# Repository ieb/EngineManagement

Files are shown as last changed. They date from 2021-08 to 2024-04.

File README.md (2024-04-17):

# Engine Management 

In July 2021 my boat was hit by lightning. The Volvo Penta D2-40 MDI unit that manages the Engine, a Volvo Penta D2-40F failed badly leaving the starter motor engaged and nearly causing an engine fire.

# Main control board

Update 20240417: In service, no issues after 3 years.

(see pcb/EngineManagementSimpleWithRelays.sch )

This project is based on the standard wiring for the core engine which is a Perkins 100. In that form the engine is controlled by switches, relays and a few flyback diodes. The only part of the original engine control that survived the strike was the Volvo Penta buttons, so those are used by a control board with pnp transistors driving relays triggered by the original buttons pulling the base of the pnp to ground. PushOn/PushOff is provided by a latching relay unit based on a LED control chip that draws a few uA when off. The control circuit draws 0.5A max and is protected by a 5A fuse and 600W TVS which will blow the fuse in the event of a voltage surge.

The main relays for Start, Stop, Glow and aux are all standard iso 40A automotive relays, each circuit fused with a suitable fuse. 

There are basic alarms for oil pressure, charge and temperature with the temperature alarm using a differential op amp with high gain adjusted to turn on a pnp at a set temperature. These all drive a buzzer with LEDs to indicate the alarm. 

A standard Tachometer sensing from the alternator W+ provides rev and engine hours. These are almost disposable being 30 GBP on eBay from many sources, all 85mm same as the Volvo Penta Tachometer.

## Mosfet alternative

Update 20240417: The PCB was prototyped, but never put into service since the relay based control board has proved 100% reliable and in service for 3 years. This section is for reference.

Although the original MDI failed due to the MOSFETs going short circuit, and in this respect relays may be more robust, it should be possible to protect MOSFETs or at least fail safe.

A 1.5KW TVS (eg SMCJ14A) with a 14.0V revers standoff, 15.6V minimum breakdown will conduct 5A@16V, 10A@18V and 40A@20V, which makes it viable as protection for excessive voltages upto 40A current, aiming to blow a fuse at above those voltages. Each mosfet needs its own TVS + suitably sized fuse or breaker. In the event of a strike or surge the TVS will short and blow the fuse before damage is done even if the MOSFET is shorted. It wont work for currents greater than 40A without exceeding the max Vds voltage of the MOSFET below.

A SI7137DP-T1-GE3 has an on resistance of 0.0016 Ohms and will dissipate < 640mW for 20A when fully on. It, unfortunately has a Max Vds of 20V and Vgs of 12v so needs protection, but provided its protected represents a robust solution as a high level switch. 

In the relay board on/off was provided by a eBay relay board which used a LED controller. To keep the number of daughter boards to a minimum and save space this is replaced by a MAX15054 on-off controller driving a N-Channel mosfet which when turned on draws the gate of one of the SI7137's to near zero turning it fully on. The same N-Channel mosfet enables P-Channel mosfets connected to the gates of other SI7137s. When the VP buttons are pressed the gates of these mosfets are dragged down to 0v turning them on, and since the N-Channel mosfet is conducting the gate of the respective SI7137 is also dragged to 0v switching that mosfet on. All P-Channel gates are pulled to +ve, and all N-Channel gates are pulled to 0v. The SI7137 has a max source gate voltage of 12v and so a 10v zener with forward diode ensures that never gets over 11.5v. 

Simulations indicate that the power dissipation in the SI7137 at 20A is 2.5W, so a pair are used for the glow plugs. At 8A for the start and stop solenoids power dissipation is closer to 500mW. Board cooling pads are used, although it might be necessary to add chip heat sinks.

Since the SI7137 are 1/10th the size of the relays, the switching circuit and NMEA2000 interface controller will all fit onto a single 10cm x 15cm board (which is the size I have in stock).

All of the silicon components were available at Farnell except the SI7137's which were ordered from Mouser, airmailed from California. For some reason RS in the UK had no stock of any mosfets.

see pcb/EngineManagementWithMosfets.sch which includes a sub-sheet of the NMEA interface. There are LTSpice simulations in pcb/simulations/ of the mosfet layout confirming transient behavior, currents and power dissipation.

Since its likely that when there is a voltage spike something on the board will blow, assuming this board works, I'll probably make a batch and keep a few spares onboard the boat.

# NMEA2000 Interface

Update 20240417: In service, minor issues after 3 years, mostly surrounding message frequency and how to some parameters to display on standard instruments.

(see pcb/EngineManagement.sch)

The standard MDI talks J1939 which is the Diesel engine CAN standard protocol. Normally this communicates with other Volvo Penta instruments, but in my case this was only the Tachometer. The J1939 Volvo Penta Tachometer did not survive the strike. The CAN bus interface was destroyed, even though there was an attempt to protect if from surges. At over 500 GBP to replace, I decided to stick with the non J1939 tachometer from eBay. For details on how to drive J1939 see the main_deprecated.cpp file. Volvo Penta service technicians probably query the MDI for fault codes, but for owners there is limited benefit where the only unit is a tachometer or basic instruments.

Once I discovered the VP Tachometer was not repairable, a separate mechanical diesel to NMEA2000 board was designed and built around an Arduino Pro Mini (Atmel 328p MCU), MCP2515 CAN controller board and some passive components. There is just enough space on 328p to hold the code and run the controller and the data collected and emitted can be displayed on any NMEA2000 instrument (eg Raymarine e7 MFD).

Component cost of the boards is probably less than 30 GBP, hence spares boards can be carried and in the worst case the engine can be controlled manually.

Replacing the blown VP parts with OEM parts would have been 1500 GBP with a further 1500 GBP required for the spare set, safe in the knowledge that a EM pulse from a near strike would result in precisely the same failure and risk of engine fire.

## NMEA2000 Messages

A D-2/40 is not exactly performance. Its not going to rev up quickly and so periods of 100ms are not really necessary for rapid engine. Same with temperatures which are really not going to change that fast. 5s is plenty fast enough.  10s is too long and most instruments treat this as no data sent.

* pgn 127488 rapid engine, 500ms
* pgn 127489 dynamic engine 1s  oil temperature == alternator temperature.
* pgn 127505 tank level 5s, instance 0 fuel type 0 diesel 
* pgn 130316 temperatures 5s,  instance/source 0/14=Exhaust, 1/3=EngineRoom, 2/15=Alternator.
* pgn 127508L battery voltage 1s, instance 0=engine battery, voltage only. instance 2=Alternator, voltage and temperature

The main battery as its now LiFePO4 with a serial to BLE module providing very detailed information. A CAN interface to this could be implemented, but the standard android app gives more than enough information and is lower power.  The original battery sensor mechanism didnt work well due to slight differences in -ve potential at the battery terminals. Hence the N2K interface only monitors Engine Battery and Alternator voltages. With a LiFeP04 battery, alternator temperature has become more important. Alternator load is controld via a Sterling A2B 120A converter which actively monitors and protect the alternator from excessive load.

# Sensors

The standard  VP flywheel pickup produces 415Hz 20V pk2pk puses with sharp edges at idle, however the signal is noisy and so it needs to be conditioned. A Schmidt trigger using an OpAmp set up positive feedback to reduce hysteresis. The positive input uses a RC network acting as a low pass filter reducing the sensitivity as the rpm rises, eliminating high frequencies ( > 10KHz). On the negative a RC network smooths the input voltage to find the mean allowing automatic offset compensation. The time period constant of the -ve input is >> than the +ve.  The inputs are via 22K resistors with the voltage measured over 100K. There are 2 chopper diodes to limit the input voltage to no more than 1V.

Using a 358 opamp with 5V supply the square wave out is 3.7V high and 0.7v low, which is just enough (3.5v being logic high), 1.5 below Vcc isn't great for an OpAmp, however 3v is high on an Arduino.

The frequency is measured by timing 10 pulses using micros().

The previous attempt without a Schmidt Trigger failed to work reliably due to noise.

The standard VP oil pressure switch is a simple switch that closes when the oil pressure drops below a threshold.

The standard VP coolant temperature sensor is identical to almost every other coolant sensor, with about 1743R at 0C and 22R at 120C. When about 33R (105C adjustable) is measured the alarm is triggered.

The charge alarm uses the voltage across the resistor supplying current into the alternator excitation coil, analogous to the charge light in cars long before there were computers.

The NMEA2000 interface board also measures fule level (0R-190R), battery voltage, alternator voltage, and 3 NCT inputs. Inputs are protected with capacitors and 100K resistors to limit current.

# Outputs

The relay board provides outputs for starter motor, stop solenoid, glow plugs and aux 12v.

The NMEA2000 board provides NMEA2000 messages.

# Connections.

The VP wiring loom has largely been replaced except for the connection to the VP buttons. Most of the original wiring loom was melted by the starter motor, but the rest was strapped tightly to the engine risking shorts when it melted.

The control box will be mounted outside the engine bay where temperatures are considerably lower (typically < 30C vs often > 85C next to the engine).

# Code

Code is all in main.cpp rather than a classes since there is little to it and I needed tight control over memory usage (less risk of hidden bloat). NMEA support uses 

	https://github.com/ttlappalainen/NMEA2000.git
	https://github.com/ttlappalainen/NMEA2000_mcp.git
	https://github.com/ttlappalainen/CAN_BUS_Shield.git

however there are some patches required, see src/*.patch. 
src/CAN_BUS_Shield.patch. The SPI clk was heavily distorted at 8MHz with a Pro Mini so I dropped the SPI to 1MHz to get a clean clk square wave. 

src/NMEA2000-library.patch The memory savings (see NMEA2000_CompilerDefns.h) which are required to run on a 382p dont compile without this patch. Additionally there I needed feedback on serial of failed packets without enabling all packet output.

Both patches must be applied if pulling fresh dependencies. 

# Memory usage

Building .pio/build/pro16MHzatmega328/firmware.hex
Advanced Memory Usage is available via "PlatformIO Home > Project Inspect"
RAM:   [==        ]  18.4% (used 377 bytes from 2048 bytes)
Flash: [========= ]  89.4% (used 27458 bytes from 30720 bytes)

If debugging of the sensors is enabled, then NMEA2000 output may have to be disabled to get the code to fit into FLASH. No problems seen with RAM at the moment, but it hasnt been tested on a live NMEA2000 bus yet.

## Update on memory.

Memory usage has proved a problem. The NMEA2000 library was designed for chips with more memory than a Pro mini and although it will run, it runs out of stack and heap when dealing with ISO Reqeusts, causing the cpu to lock up or crash. It is possible to greatly reduce memory usage by limiting buffer sizes but this truncates the responses ot the ISO requests. I think the underlying problem is that the NMEA2000 library uses temporary buffers allow it to use interrupts and to support TP packets.

So, the code is now switched to a smaller SNMEA2000 library. This only uses an 8 byte buffer for sending and is written to load that buffer, sending when full. It supports standard packets and fast packet messages. It doesn't support interrupts and is a lot simpler. 

Building with debug enabled all in ram gives
RAM:   [===       ]  32.2% (used 659 bytes from 2048 bytes)
Flash: [====      ]  37.4% (used 11492 bytes from 30720 bytes)

Initial tests indicate 1292 bytes ram available at all times when running, compared to the < 60 bytes reported with the smallest viable NMEA2000 configuration. Most of the implementation is informed by the NMEA2000 code and functionality for each use is by extension only. To reduce the work load on a polling only interface to the MCP2515 message filters are implemented on receive. It only supports a MCP2515 over SPI and will only run on an AVR based chip as it assumes little endian.

The code has, or is being verified talking to a ESP32 + MCP2562 running the NMEA2000 device analyzer.

# Changes

* 20240417  Reduced the periods for battery and fuel to 5s from 10s as N2K instruments were showing -.- periodically.
* 20240417  Output Alternator temperature to Engine Oil Temp and a dedicated "battery" (no 2) for display. Oddly no standard PGN for an DC alternator available.

# Todo/Status Relay Board

[x] Build prototype PCB and populate.
[x] Test on/off sequence.
[x] Test 20x4 I2C display.
[x] Test port extender. - discovered Can board back powers 5v switched line, added blocking diode.
[x] Connect 8 way relay board and test.
[x] Verify CAN board working.
[ ] Connect test harness sensors and test.
[FAIL] Connect VP Taco and test with simulated engine - the VP Taco is blown internally, CanH at 5V, CanL and 0V. Inside three is a large Asic which looks like it directly controls the Can bus. Very unlikely to be 
able to repair. Google for the numbers turns up no chips, and none of the other chips are CAN related.

[x] Design build and test simple relay controller unit with no MCU
[x] Design build NMEA2000 controller board
[x] Test NCT readings,  - adjusted to 4.7K top R and rebuilt NTC table from base equations.
[x] Test coolant readings - tested with fake NTC sensor wiring, need full test on real sensor
[x] Test fuel level readings
[x] Test voltage readings
[x] Test coolant with variable voltage.
[x] Test RPM with signal generator
[x] Test NMEA2000 output
[x] install
[x] Test output on MFD, all working except Charge alarm sounds all the time and RPM sensor is unreliable.
[x] Fix RPM sensor, using Schmidt trigger
[x] (disabled) Fix charge sensor, adjust resistors or disable.
[x] Adjust temperature sensor
[x] calibrate ADCs, or at least check they are correct.
[x] Test again.
[x] Install check RPM with strobe
[x] Fix fuel and voltage periods, 10s too long for N2K instruments, dropped to 5s.
[x] Output alternator temperature as oil temp, dedicated "battery" instance 2.

# Todo Status Mosfet board

This has been put on hold as the relay board works well other than the charge and temperature alarms whcih are too sensitive. Same mosfets have been used for a high current remote switch and appear to produce almost zero heat dissipation.

[x] Simulate everything in LTSpice
[x] Layout PCB
[ ] Mill prototype
[x] Order Silicon
[ ] Build prototype
[ ] Test on/off
[ ] Test other buttons and circuits, under load ideally.
[ ] Test warning circuits
[ ] Test sensors
[ ] Test NMEA2000 output
[ ] Install
[ ] Test running
[ ] Order boards and build spares.

# CanDrivers

# AVR -> MCP2515 -> TJA1050

TJA1050 runs on 5V but can take 3 or 5v logic in.
MCP2515 will run on 3v or 5v On 3v it will need a 1K/10K divider to take TJA1050 out from 3.6v to 3.3v

Scope output for this setup on 5V is very clean

# ESP -> TJA1050

TJA1050 runs on 5v with a divider on RX out to take Vrxh to 3.3v, may be easier than a MCP2562, although the output from a MCP2562 is not nearly as clean.

This setup works. Output is very clean, however the mean voltage is sensitive to the 5V supply being exactly 5V.

# Pi -> MCP2515 -> TA1050

Same as 3v AVR 3v.
Would also need a RTC, DS3231  with a LI charger TP4056
Not done as was able to fit everything I wanted into a ESP32 running a http server which draws < 40mA when not transmitting on WiFi, see CanDiagnose project.

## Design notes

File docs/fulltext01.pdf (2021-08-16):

# DISSERTATION

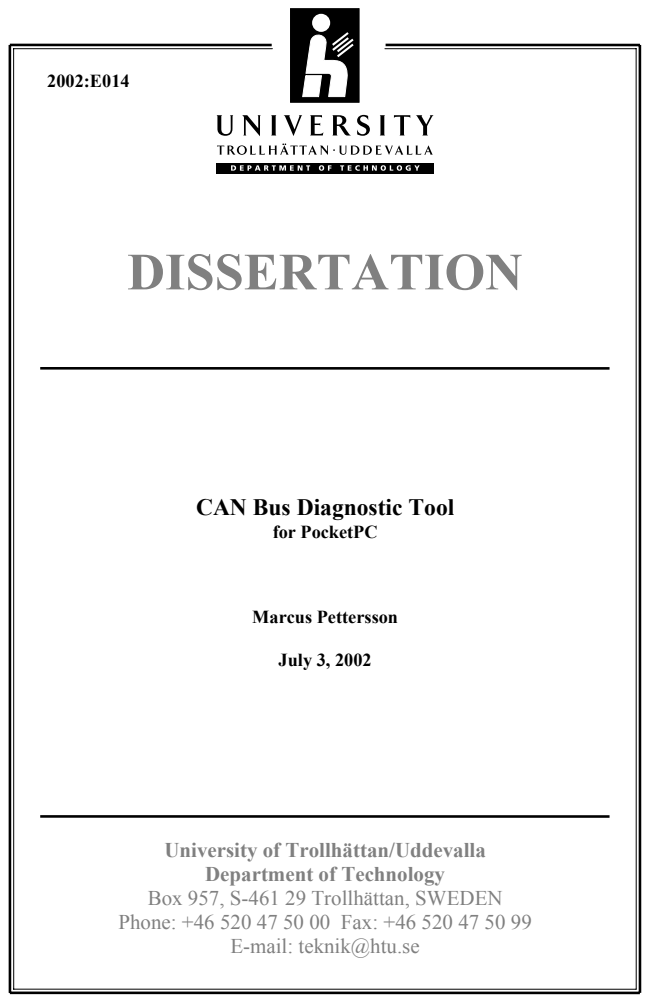
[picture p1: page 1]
for PocketPC; Marcus Pettersson; July 3, 2002

CAN Bus Diagnostic Tool

University of Trollhättan/Uddevalla
Department of Technology
Box 957, S-461 29 Trollhättan, SWEDEN
Phone: +46 520 47 50 00 Fax: +46 520 47 50 99

E-mail: teknik@htu.se

- i -

## DISSERTATION

## CAN Bus Diagnostic Tool

for PocketPC

Summary

Today’s development, where almost everything related to engine control is electronic, there is an urgent need for development of new fault searching tools. The old mechanical engines are phased out being substituted by fully electronic engines e.g. with CAN bus systems. This it is a very rapid process that put demands on human resource development as well as tool and systems used. Volvo Penta has chosen to develop those tools on a PDA (Personal Digital Assistant) platform, instead of using a traditional computer or laptop. The objective is to make life easier for service engineers by providing small and easy-to-use hand-held devices. For this purpose Volvo Penta wanted to develop a prototype software that read, analyze and display the information from the CAN data link SAE J1939. The software was developed with eMbedded Visual C++, adapted for PocketPC, or better-said Microsoft Windows CE. For the first phase this software was developed for Volvo Penta engines with EDC and EMS because they all rely on CAN SAE J1939. We decided to name the application “CAN Bus diagnostic tool for PocketPC”, same as the title of this dissertation.

Keywords: CAN, SAE J1939, PDA

Publisher: University of Trollhättan/Uddevalla, Department of Technology Box 957, S-461 29 Trollhättan, SWEDEN
Phone: + 46 520 47 50 00 Fax: + 46 520 47 50 99 E-mail: teknik@htu.se
Author: | Marcus Pettersson
Examiner: | Bo Svensson
Advisor: | Esbjörn Sjöberg, AB Volvo Penta
Subject: | Electrical Engineering, Information Systems
Language: | English | Number: | 2002:E014 | Date: | July 3, 2002

CAN Bus Diagnostic Tool

## Foreword

This dissertation “Can Bus Diagnostic Tool for PocketPC”, have been performed at AB Volvo Penta in Sweden, Gothenburg. The proposal for the dissertation comes from Anders Näzell and via Esbjörn Sjöberg it was given to me. Esbjörn Sjöberg has been my supervisor, he has helped and supported me during this dissertation.

Examiner and supervisor at University in Trollhättan/Uddevalla, has been Bo Svensson at Department of Technology.

Above all I want to thank Tobias Rasmusson at Newmad Technologies AB who helped me get going with embedded Visual C++ when we decided to change programming language from Visual Basic to Visual C++. He also gave a helping hand sorting out some programming problems and answering questions. I also want to thank Henrik Fagrell, at Newmad Technologies, that had me connected with skilled programmers at Newmad Techonologies - Tobias Rasmussen and Jonas Larsson.

Many thanks also to Product Development that gave me access to their test laboratory and by that, there test equipment so I could test the program that was developed; Anders Johansson, Anders Holmström, Jonas Welinder and Pål Loodberg.

Last, I want to thank all involved at AB Volvo Penta, everyone at unit Customer Support, and especially my supervisor Esbjörn Sjöberg.

- ii -

CAN Bus Diagnostic Tool

## Table of Contents

- iii -

CAN Bus Diagnostic Tool

## List of Symbols

API stands for Application Programming Interface

CPU stands for Central Processing Unit, the key component of a computer system, which contains the circuitry necessary to execute program instructions.

EDC stands for Electronic Diesel Control

EMS stands for Engine Management System

GUI stands for Graphical User Interface, is the software interface designed to standardize and simplify the use of computer programs.

PCMCIA stands for Personal Computer Memory Card International Association and is an external accessible expansion slot that accepts compatible cards for enhancing the computers functions.

PDA stands for Personal Digital Assistant and is a hand-held computer, often pen based that provides especially organization software as appointment calendar and communication tools.

SAE stands for Society of Automotive Engineering and is a world wide standard that almost everyone of engine-, truck-, bus-, genset-builders and so on are using today as an interface between e.g. vehicle-transmission-engine-hydraulic-systems.

- iv -

CAN Bus Diagnostic Tool

## 1 Introduction

This dissertation was performed at AB Volvo Penta in Sweden, Gothenburg where I designed an analyzer tool for their engines using CAN SAE J1939. This tool was designed for PocketPC, or more exact for a Compaq iPAQ with CAN hardware interface in terms of a PCMCIA card LAPcan II from Kvaser AB.

### 1.1 Background

The background to this dissertation is that AB Volvo Penta want to have an analyze tool for the CAN-link J1939 on a handheld computer called PDA (Personal Digital Assistant).
Today the engines from Volvo Penta are for the most part electronic and equipped with EDC, EMS or any other electronic control system. At installations of Volvo Pentas components in other manufactures products a requirement came up; the possibility to analyze what is happening in the complete installation. Concrete it meant the possibility to read what signals are inactive or active on the protocol SAE J1939, which is used to/from the control unit at Volvo Pentas products and the Customers own panels. This way you can identify errors that occur in new installations or in existing installations in the aftermarket.

### 1.2 Purpose and target

Develop an interface (tool) for installations with EMS, existing of a PDA, software and necessary cables for the connection to the application via Volvo Pentas engine cable harness at SAE J1939. The tool shall be able to capture the traffic at CAN J1939 and present the information in plain language, Swedish or English. A typical user is an educated product specialist from Volvo Penta, alternatively a well-educated service engineer that serves in the aftermarket at a service dealership.
The prototype shall be an English version with preparations to handle more languages.

### 1.3 Delimitations

The tool shall only handle engines with EMS and the prototype will only be in English. The Hardware should be Compaq’s iPAQ and necessary software will be developed for PocketPC in Visual Basic. The development platform will be Microsoft eMbedded Visual Tools with several smaller components.

### 1.4 Course of action

Learn how the CAN SAE J1939 works and how messages appear and look like. Then also learn to program Visual Basic, which was a new program language for me. During

- 1 -

CAN Bus Diagnostic Tool

the dissertations we decided to change the programming language to Visual C++, why I was forced to learn how to program Visual C++ too. Supply Volvo Penta with cable harness and connectors for SAE J1939.
Identify the messages on the CAN SAE J1939. Program a prototype that will translate the messages at the CAN to English. Documentation was written when necessary, during the dissertation.

### 1.5 Equipment

The equipment I used in this dissertation is presented in sections 1.5.1 and 1.5.2, hardware and software.

### 1.5.1 Hardware

Compaq iPAQ H3850, Compaq Expansion Jacket PC CARD For IPAQ H3XXX, Xircom CompactCard Ethernet 10 Type II
Kvaser LAPcan II – two channel CAN-controller card, two DRVcan 251 cables Computer, Dell OptiPlex GX, P2 350MHz, 192 Mb ram.
Test equipment for simulation of signals for real engine.

### 1.5.2 Software

Microsoft Windows 2000, Microsoft Office 2000, Microsoft eMbedded Visual Tools, The PocketPC 2002 SDK. Kvaser SDK and drivers for PocketPC.

### 1.6 Changes in condition

From the beginning AB Volvo Penta decided that the program should be written in Visual Basic. It was also the intention to use another hardware or CAN interface. The CAN interface that should have been used is manufactured by a company named Setek, but they were not ready when we needed it. Then we looked into alternative solutions, and found a CAN interface from Kvaser, a PCMCIA card named LAPcan II. When we got that card we found out that the programming libraries for Visual Basic wasn’t compatible with eMbedded Visual Basic for PocketPC
We then discussed the possibility to develop a dll that could be called from within Visual Basic. This never became a real alternative, since it is hard to develop a dll with no previous experience of it.
The decision was then to leave eMbedded Visual Basic for eMbedded Visual C++. I thought that was the best alternative, because eMbedded Visual C++ is much more adapted to programming on PocketPC.
- 2 -

CAN Bus Diagnostic Tool

## 2 CAN data link

Here facts are being described regarding the CAN data link.. About the CAN data link I have described some facts from standard, about the data messages and how you read the messages from the data link.
In order to develop an analysis tool for the CAN J1939, you need to know the basic principles of J1939. For that reason and to learn how it works, I had to study the standard document for CAN J1939, SAE J1939 and some other literature.

### 2.1 CAN J1939

The J1939 is the most used standard in the heavy vehicles industry. The first specification of J1939 came 1994. J1939 is based on the CAN protocol and it handle completely or partly, services from the application and transport layer and lower, according to Figure 1.5.2-1.

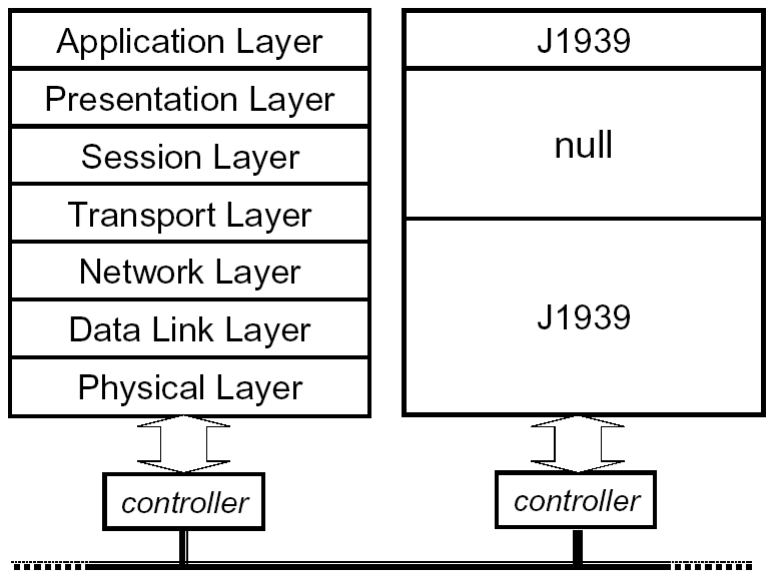
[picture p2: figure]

Figure 1.5.2-1 - The OSI model for SAE J1939

- 3 -

CAN Bus Diagnostic Tool

The functionality of each layer is:
1. Physical — Concerns the transmission of structured bit stream over physical media; deals with the mechanical, electrical, functional, and procedural characteristics to access the physical media
2. Data Link — Provides the reliable transfer of information across the physical layer; sends blocks of data (frames) with the necessary synchronization, error control, sequence control, and flow control;
3. Network — Provides upper layers with independence from the data transmission and switching technologies used to connect systems; responsible for establishing, maintaining, and terminating connections;
4. Transport — Provides reliable, transparent transfer of data between end points; provides end-to-end error recovery and flow control; provides segmentation and reassembly of very large messages;
5. Session — Provides the control structure for communication between applications; establishes, manages, and terminates connections (sessions) between cooperating applications;
6. Presentation — Provide independence to the application process from differences in data representation (syntax); and
7. Application — Provides access to the OSI environment for users and also provides distributed information services.

Bus access by message priority
- CSMA (Carrier Sense Multiple Access) / CR (Collision Resolution) Bus access conflict is resolved by arbitration
- Bit-wise
- Non-destructive
- Guaranteed latency time
CAN has no node addresses, every node receive every message and decides itself whether to use it or not. It also has an extensive error checking, with five different checks. Every connected node participates. The data consistency is secured in the way that all nodes or none accept a message.
Different Bus Management Methods can be applied for CAN systems, for example;
- Bit-wise arbitration
- Master/Slave
- 4 -

CAN Bus Diagnostic Tool

- Daisy Chain
- TDMA
CAN is only a low level specification, that means that a higher layer protocol always is required. The capability of CAN is restricted by the higher layer protocol chosen;
- Market segment
- Real-time requirements
- Product Administration requirements, etc.
For Priority and/or Identification the CAN J1939 can use 11-bit as you can see in Figure 1.5.2-2 or 29-bit as shown in Figure 1.5.2-3.

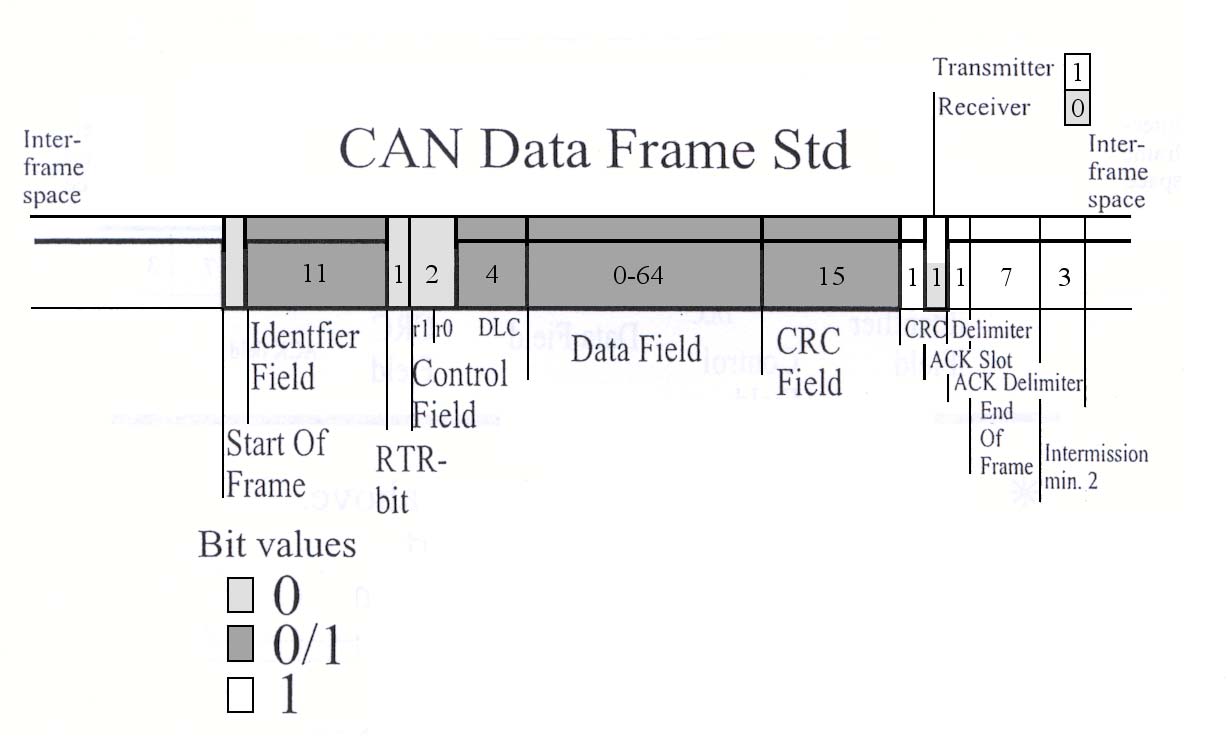
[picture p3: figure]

Figure 1.5.2-2 - CAN 11bit identifier

- 5 -

CAN Bus Diagnostic Tool

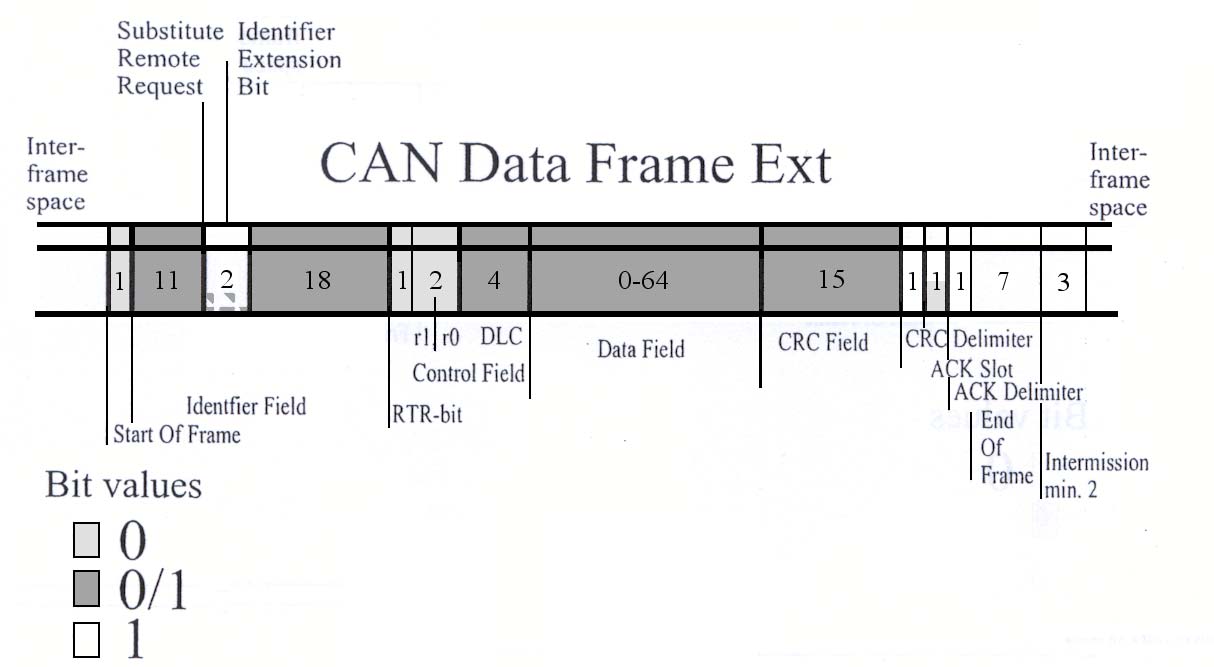
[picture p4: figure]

Figure 1.5.2-3 - CAN 29bit identifier
The 11-bit identifier is standard and the 29-bit is the extended version. Volvo uses the extended frames.
The arbitrations are done or performed in the identifier part and it also sets the priority of the message. The Remote request bit (RTR) is a part of this field. CAN-controllers often support this identification of the message by filtration.
In Control and Data length fields resides the main function Data Length Code (DLC). DLC can have values from 0 to 8. Values from 9 to 15 are not allowed. Two bits of the control field are used to indicate extended frames. When you use standard frames these bits are reserved fixed dominant.
The Data field or Message field can be from zero to eight byte, and it is always a full byte with 8-bits. These bytes can have any value. Some CAN controllers can extend ID filtration into the data field.
The CRC field is a checksum of the bits in the message and it is also optimized for this type of message. The CRC check is only one of the error checks in the CAN communication.
Acknowledgment field is to secure at least one receiver, the transmitter sets it to 1 and the receiver sets it to 0. Then you have fixed value bits, which have a fixed value for every message frame. [1]

### 2.2 Data Messages at CAN J1939

Data messages sent at CAN J1939, is surrounded with various identifier and control fields, according to previous caption CAN J1939. This message contains the data field with the signals and this message is 8 bytes. The signals are both transmitted and

- 6 -

CAN Bus Diagnostic Tool

received by the EDC. It is ten messages that have to be identified and then worked up on bit level and then viewed at the display. Just two of them are Volvo Penta specific and are called VP Status and VP Engine Industry. You can read about them in chapter 2.2.1 and 2.2.2. The other eight is according to the SAE J1939 standard document. All those messages including VP Status and VP Engine Industry are technically described in Appendix A and Appendix B.

### 2.2.1 VP Status

VP Status has 7-8 signals, which depends of the engine type we want to analyze. This type contains of the following signals; Start request that indicates if you want to start the engine, Stop request is the opposite and therefore a stop signal. Governor mode request (depends on model) indicates if the engine shall operate in engine speed mode or droop mode. This message also indicates if you selected the engine to run at idle speed. You can also see what frequency you have selected (either be 1500 rpm or 1800 rpm), in other words what engine speed in rpm that is chosen for engine operation. You can also se the status of the diagnosis switch and preheat request (not used in genset specification). The last signal is the throttle position, which is viewed as a value between 0-100 (%). [7, 8]

### 2.2.2 VP Engine Industry

This message consists of 12-13 signals depending on which engine we are analyzing. It contains of a preheat indication (depends on model) and an indication whether the engine is running or not. The running indication shows if the engine is running and has a work interval that starts at 5% below nominal engine speed, consequently 5% below 1500 rpm or 5% below 1800 rpm. Then there is also some alarms: Overspeed alarm, oil pressure alarm, oil temperature alarm, coolant temperature alarm, coolant level alarm and finally the charge alarm. VP Engine also contains indications as buzzer, general lamptest, buzzertest / lamptest, EMS Diagnose Yellow lamp and EMS Diagnose Red lamp. [7, 8]

### 2.3 CAN controller

The CAN controller interface that is used with the Compaq iPAQ H3850 is one LAPcan II PCMCIA card from Kvaser AB, and two DRVcan 251 cables because the card has two channels. From the beginning, the intention was to use a the CAN controller interface from SETEK Elektronik AB, but they did not have their interface ready in due time for this project, and even so, there would not have been so many copies of it. For those reasons we chosed the Kvaser products..

- 7 -

CAN Bus Diagnostic Tool

### 2.3.1 LAPcan II controller card

The CAN controller LAPcan II is a PC card (PCMCIA) with two channels. It has dual Philips SJA1000 CAN controllers, and it has a high performance microprocessor, memory architecture and has according to the manufacturer enhanced ESD robustness. [11]

### 2.3.2 DRVcan 251 cable

The DRVcan 251 is a combinated cable, connector and CAN driver for the LAPcan PCcard CAN interface. The DRVcan 251 contains an industry standard, high-speed CAN driver circuit. It uses a high-speed, up to 1 Megabit/second. [11]

## 3 Volvo Penta engines

Here I give an overview about the most elementary facts for the engines. This software is made for the engines that are for the most part electronic and equipped with EDC, EMS or any other electronic control system.

### 3.1 EMS – Engine Management System

This means that an electronic unit controls the engine. Engine starter and injectors are controlled by the engine management system. The following data is measured for calibrating optimal amount of fuel and used for control strategy:
- Engine speed, measured both on cam wheel and flywheel
- Boost pressure
- Boost temperature
- Coolant Temperature
- Oil Pressure
- Oil Temperature
- Fuel alarm; summer alarm indicating water in fuel or low fuel pressure
- Coolant level
The engine management system uses two different data links for communication.
- SAE J1939 (CAN) for engine control & engine monitoring.
- SAE J1587 for diagnosis, software download, parameter setting, back-up start, stop, speed control (All-speed engines).
- 8 -

CAN Bus Diagnostic Tool

The system also has some control functions: Injection control, Engine protection and Cylinder balancing.
- Injection control
Precise calculations of amount of fuel and timing of injection. This gives powerful response with virtually no smoke and low emissions.
- Engine protection
When needed, the engine will automatically shut down or decrease delivered torque in order to not get damaged.
- Cylinder balancing
The control system compensates for production differences of injectors during idle speed.
Coolant temperature: | Shut down (97-103 °C).Coolant level: Shut down.
Boost temperature: | Shut down (85 °C).Oil temperature: Shut down (122- 132 °C).
Oil pressure: | Shut down (2,2 / 0,4 Bar at 1500/Idle)Water in fuel: Error code, no decrease
Low fuel pressure: | Error code, no decrease

Engine protection All-speed
Coolant temperature: | Shut down (3-4sek) (97-103 °C).Coolant level: Shut down.
Boost temperature: | Decreasing to 50% power increasing to full power when temp is decreasing (102 °C). (Powerpac: Shut down at 102 °C).
Oil temperature: | Decreasing to 50% power, increasing to full power when temp is decreasing 122-132 °C). (Powerpac: Shut down at 122-132 °C).
Oil pressure: | Shut down (2,2 / 0,4 Bar at 1500/Idle).
Water in fuel: | Error code, no decrease
Low fuel pressure: | Error code, no decrease
Those engines have some built-in system functionality. Engine starter control is a way of achieving safe starting procedure. Further, the engines are prepared for electronic transmissions. [9]
- 9 -

CAN Bus Diagnostic Tool

### 3.2 D12 Interface

There are 3 different interfaces on the D12-industry engine, both genset and all-speed. They are as follows.
- SAE J1939 CAN-link
- CIU
- Stand alone connections

### 3.2.1 CAN link J1939

When using this link the Customer buys the engine as it is. No additional cables or senders are needed. What the Customer needs from VP is the Technical Regulation document 874423 for genset and 874424 for all-speed that describes what the protocol looks like (see an extract in Appendix A). With this document the Customer can design his own CAN-system to his control panel. Everything is included on the CAN-link, e.g. start, speed adjustment, alarm, gauges and diagnostic codes (flashing lamps). You can also see chapter CIU-interface 3.2.2. [5, 6]

### 3.2.2 CIU

If the Customer doesn’t want to be connected directly on the CAN-link he can choose to have the CIU (Control Interface Unit). This device converts the CAN-protocol to analogue/digital signals and analogue/digital signals to the CAN-protocol (see picture below). The CIU’s options are identical as on the CAN-link. [5, 6]

### 3.2.3 Stand alone connections

The stand alone connections is hard wires only, i.e. analogue and digital signals, no CAN-link available. This interface doesn’t support any signals to instruments, and thus this must be installed by the Customers themselves. [5, 6]

## 4 Realization

To carry out this dissertation I had study and partly learn Visual Basic and Visual C++, and also how they work as programming languages. I have also done some studying learning how the CAN J1939 works as I have explained earlier.

### 4.1 Programming

Here I will describe the programming language I have used in this dissertation.

- 10 -

CAN Bus Diagnostic Tool

### 4.1.1 Visual Basic

Because I haven’t programmed Visual Basic earlier, I had to put a lot of work in learning how that programming language works. However it wasn’t foreign to learn a new programming language, since I have some knowledge in other programming languages like C/C++ and Fortran. The programming language is of course separated in syntax but they are often built on the same principals and thinking.
I started with studying how Visual Basic works generally. After learning Basics and realizing most imported issues, I converted the code into Visual Basic for PocketPC or really eMbedden Visual Basic that is a better explanation. At the beginning it seamed to be equal, with some small differences. But very soon I discovered that eMbedded Visual Basic was a slim version of Visual Basic with many functions missing (which I realized I had to use).
After three weeks time we decided to change programming language to eMbedded Visual C++ instead, because there were no drivers or modules from the hardware manufacture supporting Visual Basic.

### 4.1.2 Visual C++

Embedded Visual C++ is also included in Microsoft eMbedded Visual Tools software package. I have programmed C/C++ before but I discovered that Visual C++ was a bit different. So for that reason I had to spend some time learning this programming language too. After a quick look at Visual C++ I can say that it is very different towards programming Visual Basic. Visual C++ is much more developed for eMbedded systems than Visual Basic. Tobias Rasmusson from Newmad Technologies AB helped me get going with Visual C++ when we decided to use that instead. He gave me some tip and advice that I could avoid common mistakes.

### 4.2 PocketPC programming

From the beginning it was intended that the program should be designed in Visual Basic, but when the hardware manufacture of the CAN card interface didn’t support that, we decided to program in Visual C++ instead. Another idea was to write a dll I C++ that should be called from inside Visual Basic, but that idea was discarded because of recommendations from experienced programmers. They considered writing such a dll is a dissertation in itself and therefore it will take too much time because it is so much new to learn.

### 4.2.1 Database for Signals

To make this analyze tool fairly prepared for different language, it is suitable to make a database for signal names and signal identifiers. In that database you can put the language alternatives in a table. This makes it simpler for future upgrades, as you don’t

- 11 -

CAN Bus Diagnostic Tool

need to edit more then one file. The database can for example consist of two linked tables, one table for message identifier and one for language identifier, both tables contains numbers identifying message and language. Every signal message is allocates one number, which becomes primary identifier. Then you can have a number code for every language, Swedish is for example 01 and English 03 according to previous used language codes used at Volvo Penta. Unfortunately this hasn’t been implemented in the software as planned, but hopefully the final software will have that function. At least the application is prepared for it.

### 4.2.2 Reading CAN J1939

To read the CAN bus the PCMCIA card from Kvaser is used as described earlier in this report. There software or implementation library is called CANLIB and is used for reading from the CAN card.
Kvasers CANLIB API consists exclusively of functions. Most functions return a status code, which is a negative number if the call failed and a positive number if call succeeded. The drivers for Windows CE have the same API as the “ordinary” Windows versions except 7 functions.
The first call that must be performed initialize the function library. After that is done a channel must be opened. Next that needs to be done is to set parameters bus speed. When all this is done with positive status, you can start reading information on the bus. After writing or reading bus you need to go of the bus and close the channel for clean up the circuit. [2]

### 4.2.3 The Program (Can Bus Diagnostic Tool for PocketPC)

The program is built with several modules. To start with there is a main dialog that doesn’t contain any direct functions, just calls to open other dialogs. The “About” dialog doesn’t contain any functions either. However, if you open the “Settings” dialog the function getChannel is called, and then the default setting for the channel at the CAN card will be set to channel zero. You can choose whether you want to use channel one or zero and your selection will be saved with help of function setChannel. If function is cancelled setChannel will not save the value.
The dialog “canRead” calls the CANLIB library for the CAN card, initialize it and opens the channel you selected for reading. Next you have to decide whether you want to start reading CAN bus through selected channel or open the “viewSettings” dialog where you choose what messages you want to display. The “viewSettings” dialog is a so called modeless dialog which means that the user can supply information, in this case what messages to viewed, and return to the previous task without closing the dialog box. It is possible to start the reading without choosing a message to view, but then it doesn’t write something either.
- 12 -

CAN Bus Diagnostic Tool

The viewing of the messages is put through a filter, which decides whether the message will be displayed or not. Not selected messages are discarded, which saves CPU usage (the importance of this became obvious to me during the development). When you chose to close the “canRead” dialog it also closes the CAN card channel and cleans up the buffers it may have used.

### 4.2.4 GUI (Graphic User Interface)

The Graphic User Interface is done as simple as possible. The program has one main dialog, where you can choose between “CanBusRead”, “Settings” or “About”. The “About” dialog just shows information about the program and then it will return to the main dialog. If you choose “Settings” you get to a dialog where you can choose what channel you want to use on the CAN card. There is also an option to choose what language you want to use (not in use). If you choose “CanBusRead” you will get to a dialog where the signals will be shown. You must choose what message you want to display before starting reading. As default there are no messages displayed and you can only show one message at the time at this moment. When one message is chosen to be displayed, you go back to the “CanBusRead” dialog and there the signals will be displayed. As said, this is a very simple design. This is just a simple description and illustrations (screenshots) can be found in Appendix C.
When you build a Graphic User Interface for a PDA there are some limitations. The screen is not “unlimited”, it is a very small space compared with an ordinary computer. The space you can use is 240x320 pixels, as you can se in an example in Figure 4.2.4-1.

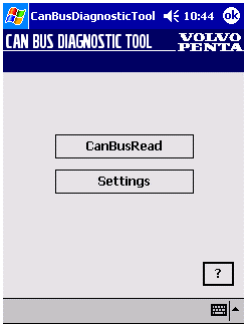
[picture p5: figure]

Figure 4.2.4-1 – Example of screen size

- 13 -

CAN Bus Diagnostic Tool

### 4.2.5 First version

The first version of the program that I wrote worked but it was really very slow. That was because all data that was read was treated at bit level. This meant that every message that was sent out had a short delay with approximately 4 seconds. This resulted in a search for possible solutions to this problem. First I thought all messages were buffered before being displayed, why I tried to empty the buffer. Soon I realized that this wasn’t a solution to the problem, instead the idea came up to filter messages before they were processed at bit level. This is how the second version is constructed.

### 4.2.6 Second version

The second version has precisely the same bit filtering for viewing signals, because that worked without any problem. The difference is, here I have a filter that doesn’t care about the messages I don’t want to show, why they are deleted immediately. This version also has another thread then the first version, and hopefully this made the messages appear faster. This should have the consequence that the whole program would work faster. Unfortunately I haven’t been able to test more then two messages properly, and that was the EEC1 with the engine speed and the VP Status with for example Throttle position. These messages were now updated much faster then before, approximately with a delay less than one second. But there are still some bugs. Updates to screen works for about 30 seconds or up to a minute and then it stops.

### 4.2.7 Third version

After contact with Martin Henriksson at Kvaser AB, that is the hardware manufacture, I got some tips on how to get rid of the update problem and the delay. He told me, that I could try to take the “thread” away and replace it with the built-in canNotify function that is available in their drivers and CANlib library. This function sends a notification every time a message is received from the CAN data link and in this way the software don’t crash the application on the handheld computer. Because of this the delay disappeared and the update to the display worked without faults. By that the software is working very good and accordingly to targets.

### 4.3 Connection to Volvo Pentas Engine cable harness

Mission objective was to supply with cables for connecting to the engine’s cable harness. There already exists one cable for that at Volvo Penta, but that cable doesn’t have the right connector. The existing cable also needs a new connector for the tool or a new cable. Volvo Penta will later decide how to solve this problem.

- 14 -

CAN Bus Diagnostic Tool

## 5 Results

As described in the objectives the result should be a prototype software that reads the CAN bus at Volvo Pentas engines with EDC and EMS. This software is called “Can Bus Diagnostic Tool for PocketPC” and is a software that reads CAN bus and displays the result of the signals on the screen at the PDA. How the GUI (Graphic User Interface) is constructed you can see if you study the snapshots that are made from the PDA. You find them together with de block diagram in Appendix C. According to me results are very positive. It is really possible to design a tool for this purpose, for a PDA and I am really happy to have got so far in a short period of time.

## 6 Conclusions

As conclusion, you can say this result agree to objectives and what was proposed in the beginning of my dissertation. That is a prototype software to read the CAN SAE J1939 data link on a PDA. The J1939 data link is used for control and for monitoring data.

### 6.1 Analyses of the result

As conclusion you can say that I have got three different types of software prototypes, which all works but with small differences in performance. The first one reads all the defined messages and manages them all even if only the ones you have chosen are displayed. That version works with a delay of approximately 4 seconds. I think that delay depends on the program managing all the messages and at the same time. It is a proper working version, but maybe not the final solution since the delay cannot really be accepted.
The second version was thought to be faster, and the delays would be eliminated. However it looks like it has become a bit faster, there are some bugs instead. The update of the screen doesn’t work properly at all times. When testing for example the engine speed it works for approximately half a minute and then it stops updating the screen. The software however reads CAN data for the whole time and sends it further for screen update, but there is no update to be seen on the display. This software is a bit faster then the first one regarding the EEC1 and VP Status messages that was the best message to study in this case.
The third version works very good and all the delays and update problems are solved. However there is sill some small bugs but now the program works very good.
A result or conclusion of this dissertation is that I can say it’s possible to design a software like this, that works quite excellent and with more functions.
- 15 -

CAN Bus Diagnostic Tool

### 6.2 Recommendations for continues work

If Volvo Penta chooses to continue developing the software I have developed during this dissertation, there are some things to elucidate. For one thing, there must be much more testing to get rid of the small bugs there is left. Second thing would be to implement more functions, for example a log function to log the messages to a file. There are some questions, referring to Anders Näzell, about how a Compaq iPAQ manage damp, shock or a situation where you drop it. This question should be answered by Compaq, but with normal handling the selected PDA will suite its propose. A solution to this can be to put the PDA into one of many existing casings on the market. Perhaps it is also possible to have an agreement with Compaq that covers damage and other things related to using the PDA in the aftermarket as an engineer’s tool.

- 16 -

CAN Bus Diagnostic Tool

## 7 Reference

### 7.1 Books and datasheet

1 Kvaser AB Sweden, 1998, CAN

2 Kvaser AB Sweden, 2001, CANLIB SDK User’s Guide Version 3.0

3 Deitel, H. M., Deitel, P. J., 1997, C++ How to Program

4 SAE International, 1996-05, SAE J1939/71

5 AB Volvo Penta, 2001-02-01, Electrical Interface, TWD1240VE

6 AB Volvo Penta, 2001-01-30, Electrical Interface, TAD1240, 1241, 1242GE

7 AB Volvo Penta, 2000-12-14, Technical Regulation; no. 874423, Interface specification for TAD124xGE

8 AB Volvo Penta, 2000-12-20, Technical Regulation; no 8774424, Interface specification for TWD1240VE

9 AB Volvo Penta, Document made by Anders Näzell

### 7.2 Websites

11 Kvaser AB, http://www.kvaser.com, 2002-05-23

- 17 -

CAN Bus Diagnostic Tool

## Appendix

A Volvo Penta Specific messages | 13 pages
B Messages from standard SAE J1939 | 18 pages
C Overview of the program | 2 pages
- 18 -

Appendix A

## Extract from Technical Regulation, Interface

specification for TAD124xGE and TWD1240VE.

Volvo Penta specific messages

TAD124xGE
J1939 Proprietary frames
VP Engine Industry
Data Length | 8
Transmission update period | 50 ms
Data page | 0
PDU format | 255
PDU specific | 71
Priority | | 3
Source address | 0
PGN Number (calculated) | 65351
Identifier (calculated) | 218056448
Description | Engine information
Byte | Bit | Signal
1 | 1-2 | Not used
1 | 3-4 | Running indication
1 | 5-6 | Overspeed alarm
1 | 7-8 | Oil pressure alarm
2 | 1-2 | Oil temperature alarm
2 | 3-4 | Coolant temperature alarm
2 | 5-6 | Coolant level alarm
2 | 7-8 | Charge alarm
3 | 1-2 | Buzzer
3 | 3-8 | Not used
4 | 1-2 | General lamptest
4 | 3-4 | Buzzertest / Lamptest
4 | 5-8 | Not used
5 | 1-2 | EMS Diagnose Yellow lamp
5 | 3-4 | EMS Diagnose Red lamp
5 | 5-8 | Not used
6 | 1-24 | Not used
- I -

Appendix A

Running indication
The running status of the engine
Value | Description
0 | Stopped
1 | Running
2 | Reserved
3 | Not available

Type:Measured
Format: Numeric

Overspeed alarm
The status of the (virtual) overspeed alarm switch
Value | Description
0 | Inactive
1 | Active
2 | Switch error
3 | Not available

Type:Measured
Format: Numeric

Oil pressure alarm
The status of the (virtual) oil pressure alarm switch
Value | Description
0 | Inactive
1 | Active
2 | Switch error
3 | Not available

Type:Measured
Format: Numeric

Oil temperature alarm
The status of the (virtual) oil temperature alarm switch
Value | Description
0 | Inactive
1 | Active
2 | Switch error
3 | Not available

Type: Measured
Format: Numeric
- II -

Appendix A

Coolant temperature alarm
The status of the (virtual) coolant temperature alarm switch
Value | Description
0 | Inactive
1 | Active
2 | Switch error
3 | Not available

Type: Measured
Format: Numeric

Coolant level alarm
The status of the coolant level alarm switch
Value | Description
0 | Inactive
1 | Active
2 | Switch error
3 | Not available

Type: Measured
Format: Numeric

Charge alarm
The status of the (virtual) charge alarm switch
Value | Description
0 | Inactive
1 | Active
2 | Switch error
3 | Not available

Type: Measured
Format: Numeric

Buzzer
Controls the buzzer
Value | Description
0 | Inactive
1 | Active
2 | Reserved
3 | Not available

Type: Status
Format: Numeric
- III -

Appendix A

General lamptest
Controls the general lamptest
Value | Description
0 | Inactive
1 | Active
2 | Reserved
3 | Not available

Type: Status
Format: Numeric

Buzzertest / Lamptest
Controls the buzzertest / lamptest
Value | Description
0 | Inactive
1 | Active
2 | Reserved
3 | Not available

Type: Status
Format: Numeric

EMS Diagnose Yellow lamp
The status of the yellow diagnose lamp of the EMS (Mirror of PID 44, J1587)
Value | Description
0 | Inactive
1 | Active
2 | Error condition
3 | Not available

Type: Status
Format: Numeric

EMS Diagnose Red lamp
The status of the red diagnose lamp of the EMS (Mirror of PID 44, J1587)
Value | Description
0 | Inactive
1 | Active
2 | Error condition
3 | Not available

Type: Status
Format: Numeric
- IV -

Appendix A

VP Status
Data Length | 8
Transmission update period | 20 ms
Data page | 0
PDU format | 255
PDU specific | 70
Priority | | 3
Source address | 17
PGN Number (calculated) | 65350
Identifier (calculated) | 218056209
Description | CIU status information
Byte | Bit | Signal
1 | 1-2 | Start request
1 | 3-4 | Stop request
1 | 5-6 | Not used
1 | 7-8 | Idle speed select
2 | 1-2 | Frequency select
2 | 3-4 | Diagnosis switch
2 | 5-6 | Preheat request, not used in genset spec.
2 | 7-8 | Not used
3 | 1-16 | Accelerator pedal position
5 | 1-32 | Not used

Start request
Start request
Value | Description
0 | Inactive
1 | Active
2 | Error indication
3 | Not available

Type: Status
Format: Numeric

Stop request
Stop request
Value | Description
0 | Inactive
1 | Active
2 | Error indication
3 | Not available

Type: Status
Format: Numeric
- V -

Appendix A

Idle speed select
Indicates if the engine shall operate at idle speed or at running speed.
Value | Description
0 | Normal running speed request
1 | Idle speed request
2 | Error indication
3 | Not available

Type: Status
Format: Numeric

Frequency select
Indicates if the engine shall operate at primary engine speed or secondary engine speed rpm.
Value | Description
0 | Primary engine speed request
1 | Secondary engine speed request
2 | Error indication
3 | Not available

Type: Status
Format: Numeric

Diagnosis switch
Status of the Diagnosis switch
Value | Description
0 | Inactive
1 | Active
2 | Error indication
3 | Not available

Type: Status
Format: Numeric

Accelerator pedal position
The accelerator pedal position

Resolution: 0.097752 %/bit (1/1023) Offset: 0
Size: 2 bytes, bit 0-9
Data range: 0 to 100
Unit: %
Error indication: FEFF

Type: Measured
Format: Numeric
- VI -

Appendix A

TWD1240VE
J1939 Proprietary frames
VP Engine Industry
Data Length | 8
Transmission update period | 50 ms
Data page | 0
PDU format | 255
PDU specific | 71
Priority | | 3
Source address | 0
PGN Number (calculated) | 65351
Identifier (calculated) | 218056448
Description | Engine information
Byte | Bit | Signal
1 | 1-2 | Preheat indication
1 | 3-4 | Running indication
1 | 5-6 | Overspeed alarm
1 | 7-8 | Oil pressure alarm
2 | 1-2 | Oil temperature alarm
2 | 3-4 | Coolant temperature alarm
2 | 5-6 | Coolant level alarm
2 | 7-8 | Charge alarm
3 | 1-2 | Buzzer
3 | 3-8 | Not used
4 | 1-2 | General lamptest
4 | 3-4 | Buzzertest / Lamptest
4 | 5-8 | Not used
5 | 1-2 | EMS Diagnose Yellow lamp
5 | 3-4 | EMS Diagnose Red lamp
5 | 5-8 | Not used
6 | 1-24 | Not used

Preheat indication
The status of the preheat relay
Value | Description
0 | Inactive
1 | Active
2 | Error state
3 | Not available

Type: Measured
Format: Numeric
- VII -

Appendix A

Running indication
The running status of the engine
Value | Description
0 | Stopped
1 | Running
2 | Reserved
3 | Not available

Type:Measured
Format: Numeric

Overspeed alarm
The status of the (virtual) overspeed alarm switch
Value | Description
0 | Inactive
1 | Active
2 | Switch error
3 | Not available

Type:Measured
Format: Numeric

Oil pressure alarm
The status of the (virtual) oil pressure alarm switch
Value | Description
0 | Inactive
1 | Active
2 | Switch error
3 | Not available

Type:Measured
Format: Numeric

Oil temperature alarm
The status of the (virtual) oil temprature alarm switch
Value | Description
0 | Inactive
1 | Active
2 | Switch error
3 | Not available

Type: Measured
Format: Numeric
- VIII -

Appendix A

Coolant temperature alarm
The status of the (virtual) coolant temperature alarm switch
Value | Description
0 | Inactive
1 | Active
2 | Switch error
3 | Not available

Type: Measured
Format: Numeric

Coolant level alarm
The status of the coolant level alarm switch
Value | Description
0 | Inactive
1 | Active
2 | Switch error
3 | Not available

Type: Measured
Format: Numeric

Charge alarm
The status of the (virtual) charge alarm switch
Value | Description
0 | Inactive
1 | Active
2 | Switch error
3 | Not available

Type: Measured
Format: Numeric

Buzzer
Controls the buzzer
Value | Description
0 | Inactive
1 | Active
2 | Reserved
3 | Not available

Type: Status
Format: Numeric
- IX -

Appendix A

General lamptest
Controls the general lamptest
Value | Description
0 | Inactive
1 | Active
2 | Reserved
3 | Not available

Type: Status
Format: Numeric

Buzzertest / Lamptest
Controls the buzzertest / lamptest
Value | Description
0 | Inactive
1 | Active
2 | Reserved
3 | Not available

Type: Status
Format: Numeric

EMS Diagnose Yellow lamp
The status of the yellow diagnose lamp of the EMS (Mirror of PID 44, J1587)
Value | Description
0 | Inactive
1 | Active
2 | Error condition
3 | Not available

Type: Status
Format: Numeric

EMS Diagnose Red lamp
The status of the red diagnose lamp of the EMS (Mirror of PID 44, J1587)
Value | Description
0 | Inactive
1 | Active
2 | Error condition
3 | Not available

Type: Status
Format: Numeric
- X -

Appendix A

VP Status
Data Length | 8
Transmission update period | 20 ms
Data page | 0
PDU format | 255
PDU specific | 70
Priority | | 3
Source address | 17
PGN Number (calculated) | 65350
Identifier (calculated) | 218056209
Description | CIU status information
Byte | Bit | Signal
1 | 1-2 | Start request
1 | 3-4 | Stop request
1 | 5-6 | Governor mode request
1 | 7-8 | Idle speed select
2 | 1-2 | Frequency select
2 | 3-4 | Diagnosis switch
2 | 5-6 | Preheat reqeuest
2 | 7-8 | Not used
3 | 1-16 | Accelerator pedal position
5 | 1-32 | Not used

Start request
Start request
Value | Description
0 | Inactive
1 | Active
2 | Error indication
3 | Not available

Type: Status
Format: Numeric

Stop request
Stop request
Value | Description
0 | Inactive
1 | Active
2 | Error indication
3 | Not available

Type: Status
Format: Numeric
- XI -

Appendix A

Governor mode request
Indicates if the engine shall operate in Engine speed mode or Droop mode.
Value | Description
0 | Engine speed mode request
1 | Droop mode request
2 | Error indication
3 | Not available

Type: Status
Format: Numeric

Idle speed select
Indicates if the engine shall operate at idel speed or at running speed
Value | Description
0 | Normal running speed request
1 | Idle speed request
2 | Error indication
3 | Not available

Type: Status
Format: Numeric

Frequency select
Indicates if the engine shall operate at primary engine speed or secondary engine speed rpm.
Value | Description
0 | Primary engine speed request
1 | Secondary engine speed request
2 | Error indication
3 | Not available

Type: Status
Format: Numeric

Diagnosis switch
Status of the Diagnosis switch
Value | Description
0 | Inactive
1 | Active
2 | Error indication
3 | Not available
Type: Status
Format: Numeric
- XII -

Appendix A

Preheat request
Status of the Preheat request.
Value | Description
0 | Inactive
1 | Active
2 | Error indication
3 | Not available

Type: Status
Format: Numeric

Accelerator pedal position
The accelerator pedal position

Resolution: 0.097752 %/bit (1/1023) Offset: 0
Size: 2 bytes, bit 0-9
Data range: 0 to 100
Unit: %
Error indication: FEFF

Type: Measured
Format: Numeric
- XIII -

Appendix B

## Extract from standard document SAE J1939/71

SAE International SAE J1939/71, Surface Vehicle Standard – Vehicle Application Layer, Issued 1994-08, Revised 1996-05

Messages from standard SAE J1939

### 1 ELECTRONIC ENGINE CONTROLLER #2: EEC2

Transmission repetition rate: | 50 ms
Data length: | 8 bytes
Data page: | 0
PDU format: | 240
PDU specific: | 3
Default priority: | 3
Parameter group number: | 61,443 (00F00316)

Byte: 1 Status_EEC2 Bit: 8-5 Not defined
4-3 AP kickdown switch | 1.1
2-1 AP low idle switch | 1.2
2 Accelerator pedal (AP) position | 1.3
3 Percent load at current speed | 1.4
4-8 Not defined

1.1 Accelerator Pedal Kickdown Switch—Switch signal which indicates whether the accelerator pedal kickdown switch is opened or closed. The kickdown switch is defined in SAE J1843.
00 - Kickdown passive
01 - Kickdown active
Type: Measured
Suspect Parameter Number: 559

1.2 Accelerator Pedal Low Idle Switch—Switch signal which indicates whether the accelerator pedal low idle switch is opened or closed. The low idle switch is defined in SAE J1843.
00 - Accelerator pedal not in low idle condition
01 - Accelerator pedal in low idle condition
Type: Measured
Suspect Parameter Number: 558

1.3 Accelerator Pedal Position—The ratio of actual accelerator pedal position to maximum pedal position. Although it is used as an input to determine powertrain demand, it also provides anticipatory information to transmission and ASR algorithms about driver actions.
Data Length: 1 byte
Resolution: 0.4%/bit gain, 0% offset
Data Range: 0 to 100%
Type: Measured
Suspect Parameter Number: 91
- I -

Appendix B

1.4 Percent Load at Current Speed—The ratio of actual engine percent torque (indicated) to maximum indicated torque available at the current engine speed, clipped to zero torque during engine braking.
Data Length: 1 byte
Resolution: 1%/bit gain, 0% offset
Range: 0 to 125%
Type: Status
Suspect Parameter Number: 92

### 2 ELECTRONIC ENGINE CONTROLLER #1: EEC1

Transmission repetition rate: | engine speed dependent (see 3.1.6.2)
Data length: | 8 bytes
Data page: | 0
PDU format: | 240
PDU specific: | 4
Default priority: | 3
Parameter group number: | 61,444 (00F00416)

Byte: 1 Status_EEC1 Bit: 8-5 Not defined
4-1 Engine/retarder torque mode | 2.1
2 Driver’s demand engine - percent torque | 2.2
3 Actual engine - percent torque | 2.3
4,5 Engine speed | 2.4
6-8 Not defined

2.1 Engine and Retarder Torque Mode (4 bits)—State signal which indicates which engine or retarder torque mode is currently generating, limiting or controlling the torque. Note that the modes are not in prioritized order. Not all modes may be relevant for a given device. Some devices may not implement all functions. For typical priorities refer to Figures 1 and 2 for engine control and Tables 2 to 4 for retarder control. The data type of this parameter is measured.

Mode 00002 means “No request”: engine torque may range from 0 to full load only due to low idle governor output; retarder torque = 0 (no braking).

Modes 00012 to 11102 indicate that there is either a torque request or the identified function is currently controlling the engine/retarder: engine/retarder torque may range from 0 (no fueling/no braking) to the upper limit.

Suspect Parameter Number:Engine Mode: 899
Retarder Mode: 900
- II -

Appendix B

Table 1 - Engine/Retarder Torqure Modes

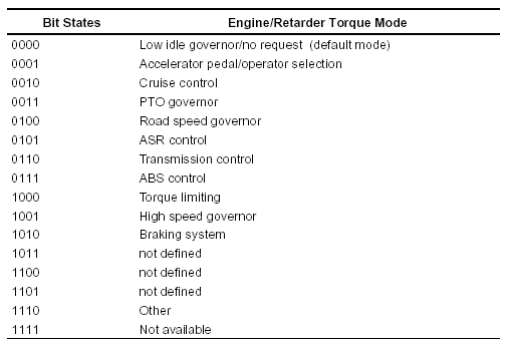
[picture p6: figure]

2.1.1 Low Idle Governor/No request (Default mode)—This mode is active if the accelerator pedal (not necessarily the torque output of the driver input, see Figure 1 and Figure 2) is zero. This is the default mode. At low speed the low idle governor may be active while at higher speed it is zero.

2.1.2 Accelerator Pedal—This mode is active if the accelerator pedal position is active (being followed). This mode is active for the retarder if it is turned on by the operator. Note that it may be disabled by the accelerator pedal or clutch switches (operator selection).

2.1.3 Cruise Control—This mode is active if cruise control is active and greater than the accelerator pedal request.

2.1.4 PTO Governor—This mode is active if the PTO governor is active.

2.1.5 Road Speed Governing—Indicates that road speed governing is active and limiting torque.

2.1.6 ASR Control—Indicates that the ASR command is active (Speed, Torque, or Speed/Torque Limit Control).

2.1.7 Transmission Control—Indicates that the transmission command is active (Speed, Torque, or Speed/Torque Limit Control).

2.1.8 ABS Control—Indicates that the ABS is controlling torque.

2.1.9 Torque Limiting—This mode is active if the demanded or commanded engine torque is limited by internal logic due to full load, smoke and/or emissions control, engine protection and/or other factors. A reduced torque limit may be

- III -

Appendix B

necessary for engine protection if the engine temperature is too high or a sensor fails (speed, timing, or boost pressure), as examples.

2.1.10 High Speed Governor—his mode is active if the engine is controlled by the high speed governor due to normal operation.

2.1.11 Brake System (Electronic)—This indicates that the brake pedal is controlling the torque. Note that this may include enabling of the retarder when the brake pedal is depressed (touched).
Note that if there is a request to the retarder but operating conditions do not allow braking, this situation will be reflected by the Percent Retarder Torque = 0 when broadcast.

2.1.12 Other—Torque control by a type of device which is different than those defined in2.1.1 through 2.1.11.

2.2 Driver’s Demand Engine - Percent Torque—The requested torque output of the engine by the driver. It is based on input from the following requestors external to the powertrain: operator (via the accelerator pedal), cruise control and/or road speed limit governor. Dynamic commands from internal powertrain functions such as smoke control, low- and high-speed engine governing; ASR and shift control are excluded from this calculation. The data is transmitted in indicated torque as a percent of the indicated peak engine torque. See 4.3.17 in standard document for the engine configuration message. Several status bits are defined separately to indicate the request which is currently being honored. This parameter may be used for shift scheduling. Data Length: 1 byte Resolution: 1%/bit gain, -125% offset (00 = -125%, 125 = 0%, 250 = +125%) Data Range: -125 to 125% Operating Range: 0 to 125% Type: Measured Suspect Parameter Number: 512

Figure 1 and Figure 2 show two typical torque calculations in an engine
| controller. On the left side of the figures there are single engine controller functions. The output torque signals of these functions are connected in the manner shown. The result is the actual engine percent torque which is realized by the engine.
- IV -

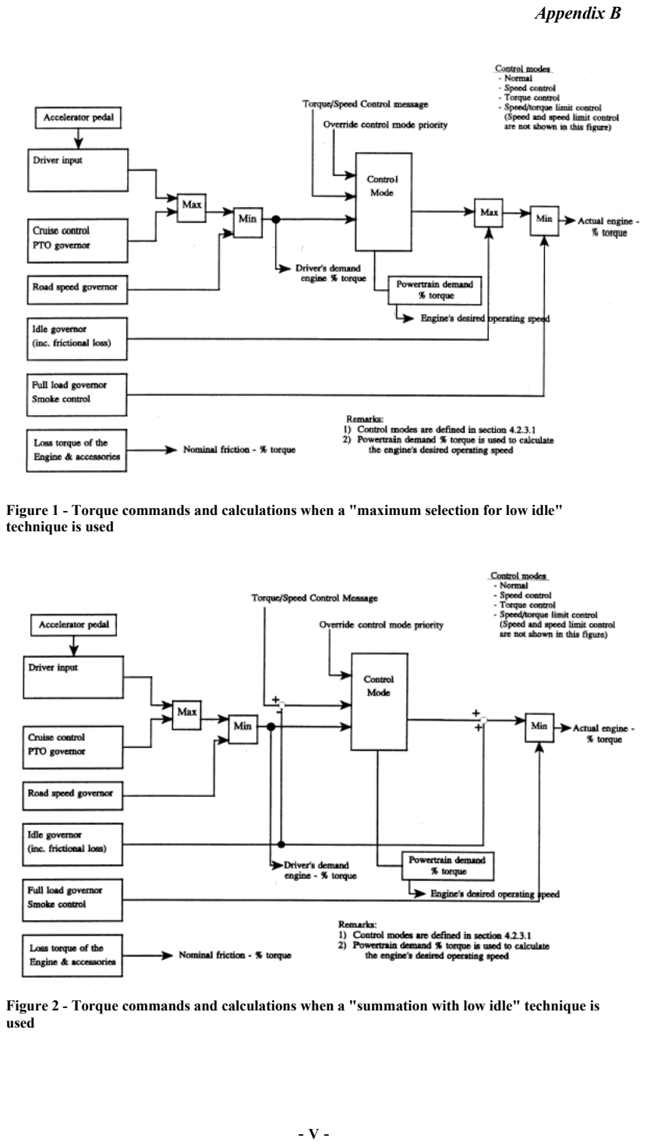
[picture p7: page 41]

Appendix B

Figure 1 - Torque commands and calculations when a "maximum selection for low idle" technique is used

Figure 2 - Torque commands and calculations when a "summation with low idle" technique is used

- V -

Appendix B

On top of the figures, external torque commands (e.g., traction and transmission control) can control the engine. These commands can influence the engine torque by four control modes. Four engine internal signals are transmitted to the network:

a. Driver’s demand engine - percent torque
b. Actual engine - percent torque
c. Nominal friction - percent torque
d. Engine's desired operating speed

The difference between Figure 1 and Figure 2 is the connection of the idle governor output to the torque calculation. In Figure 1 there is a maximum selection, while in Figure 2 a summation is used. The summation method needs a subtraction point for each external command input because the starting point of an ASR or a shift operation should be the present actual engine -percent torque value. As the actual engine - percent torque signal contains the idle governor output and the external commands are compared with the driver’s demand engine - percent torque or the powertrain demand which don't contain the idle governor output, the external commands must be subtracted by the idle governor output to get the correct signals for comparison. The advantage of the maximum selection (Figure 1) is that no other speed controller can work parallel to the idle governor. This allows for a better optimization of the different speed control loops. The advantage of the summation method (Figure 2) is that changes of the idle governor output influence the engine directly (no dead zones exist).

2.3 | Actual Engine - Percent Torque—The calculated output torque of the engine. The data is transmitted in indicated torque as a percent of peak engine torque. The engine percent torque value will not be less than zero and it includes the torque developed in the cylinders required to overcome friction as described in 4.2.1.3 standard document. Data Length: 1 byte Resolution: 1%/bit gain, -125% offset Data Range: -125 to 125% Operating Range: 0 to 125% Type: Measured Suspect Parameter Number: 513
2.4 | Engine Speed—Actual engine speed which is calculated over a minimum crankshaft angle of 720 degrees divided by the number of cylinders. Data Length: 2 bytes Resolution: 0.125 rpm/bit gain, 0 rpm offset (upper byte resolution = 32 rpm/bit) Data Range: 0 to 8031.875 rpm Type: Measured Suspect Parameter Number: 190

### 3 ENGINE TEMPERATURE: ET

- VI -

Appendix B

Transmission repetition rate: | 1 s
Data length: | 8 bytes
Data page: | 0
PDU format: | 254
PDU specific: | 238
Default priority: | 6
Parameter group number: | 65,262 (00FEEE16)
Byte: 1 Engine coolant temperature | 3.1
2 Fuel temperature | 3.2
3,4 Engine oil temperature | 3.3
5,6 Turbo oil temperature | 3.4
7 Engine intercooler temperature | 3.5
8 Not defined

3.1 Engine Coolant Temperature—Temperature of liquid found in engine cooling system.
Data Length: 1 byte
Resolution: 1 °C/bit gain, -40 °C offset
Data Range: -40 to +210 °C (-40 to 410 °F)
Type: Measured
Suspect Parameter Number: 110

3.2 Fuel Temperature—Temperature of fuel entering injectors. Data Length: 1 byte
Resolution: 1 °C/bit gain, -40 °C offset
Data Range: -40 to +210 °C (-40 to 410 °F)
Type: Measured
Suspect Parameter Number: 174

3.3 Engine Oil Temperature—Temperature of the engine lubricant. Data Length: 2 bytes
Resolution: 0.03125 °C/bit gain, -273 °C offset
Data Range: -273 to +1735.0 °C (-459.4 to 3155.0 °F)
Type: Measured
Suspect Parameter Number: 175

3.4 Turbo Oil Temperature—Temperature of the turbocharger lubricant. Data Length: 2 bytes
Resolution: 0.03125 °C/bit gain, -273 °C offset
Data Range: -273 to +1735.0 °C (-459.4 to 3155.0 °F)
Type: Measured
Suspect Parameter Number: 176

3.5 Engine Intercooler Temperature—Temperature of liquid found in the intercooler located after the turbocharger.
Data Length: 1 byte
Resolution: 1 °C/bit gain, -40 °C offset
Data Range: -40 to +210 °C (-40 to 410 °F)
- VII -

Appendix B

Type: Measured
Suspect Parameter Number: 52

### 4 ENGINE FLUID LEVEL/PRESSURE: EFLP

Transmission repetition rate: | 0.5 s
Data length: | 8 bytes
Data page: | 0
PDU format: | 254
PDU specific: | 239
Default priority: | 6
Parameter group number: | 65,263 (00FEEF16)
Byte: 1 Fuel delivery pressure | 4.1
2 Not defined
3 Engine oil level | 4.2
4 Engine oil pressure | 4.3
5,6 Crankcase pressure | 4.4
7 Coolant pressure | 4.5
8 Coolant level | 4.6
4.1 | Fuel Delivery Pressure—Gage pressure of fuel in system as delivered from
supply pump to the injection pump.
Data Length: 1 byte
Resolution: 4 kPa/bit gain, 0 kPa offset
Data Range: 0 to +1000 kPa (0 to 145 psi)
Type: Measured
Suspect Parameter Number: 94

4.2 Engine Oil Level—Ratio of current volume of engine sump oil to maximum required volume.
Data Length: 1 byte
Resolution: 0.4 %/bit gain, 0 % offset
Data Range: 0 to +100 %
Type: Measured
Suspect Parameter Number: 98

4.3 Engine Oil Pressure—Gage pressure of oil in engine lubrication system as provided by oil pump.
Data Length: 1 byte
Resolution: 4 kPa/bit gain, 0 kPa offset
Data Range: 0 to +1000 kPa (0 to 145 psi)
Type: Measured
Suspect Parameter Number: 100

4.4 Crankcase Pressure—Gage pressure inside engine crankcase.
Data Length: 2 bytes
Resolution: 7.8125 x 10-3 kPa/bit gain (1/128 kPa/bit), -250 kPa offset Data Range: -250 to +251.99 kPa (-36.259 to +36.548 lbf/in2)
- VIII -

Appendix B

Type: Measured
Suspect Parameter Number: 101

4.5 Coolant Pressure—Gage pressure of liquid found in engine cooling system. Data Length: 1 byte
Resolution: 2 kPa/bit gain, 0 kPa offset
Data Range: 0 to +500 kPa (0 to 72.5 psi)
Type: Measured
Suspect Parameter Number: 109

4.6 Coolant Level—Ratio of volume of liquid found in engine cooling system to total cooling system volume.
Data Length: 1 byte
Resolution: 0.4 %/bit gain, 0 % offset
Data Range: 0 to +100 %
Type: Measured
Suspect Parameter Number: 111

### 5 INLET/EXHAUST CONDITIONS: IEC

Transmission repetition rate: | 0.5 s
Data length: | 8 bytes
Data page: | 0
PDU format: | 254
PDU specific: | 246
Default priority: | 6
Parameter group number: | 65,270 (00FEF616)
Byte: 1 Particulate trap inlet pressure | 5.1
2 Boost pressure | 5.2
3 Intake manifold temperature | 5.3
4 Air inlet pressure | 5.4
5 Air filter differential pressure | 5.5
6,7 Exhaust gas temperature | 5.6
8 Coolant filter differential pressure | 5.7
5.1 | Particulate Trap Inlet Pressure—Exhaust back pressure as a result of particle
accumulation on filter media placed in the exhaust stream.
Data Length: 1 byte
Resolution: 0.5 kPa/bit gain, 0 kPa offset
Data Range: 0 to +125 kPa (0 to +18.1 psi)
Type: Measured
Suspect Parameter Number: 81

5.2 Boost Pressure—Gage pressure of air measured downstream on the compressor discharge side of the turbocharger.
Data Length: 1 byte
Resolution: 2 kPa/bit gain, 0 kPa offset
Data Range: 0 to +500 kPa (0 to 72.5 psi)
- IX -

Appendix B

Type: Measured
Suspect Parameter Number: 102

5.3 Intake Manifold Temperature—Temperature of precombustion air found in intake manifold of engine air supply system.
Data Length: 1 byte
Resolution: 1 °C/bit gain, -40 °C offset
Data Range: -40 to +210 °C (-40 to 410 °F)
Type: Measured
Suspect Parameter Number: 105

5.4 Air Inlet Pressure—Absolute air pressure at inlet to intake manifold or air box. Data Length: 1 byte
Resolution: 2 kPa/bit gain, 0 kPa offset
Data Range: 0 to +500 kPa (0 to 72.5 psi)
Type: Measured
Suspect Parameter Number: 106

5.5 Air Filter Differential Pressure—Change in engine air system pressure, measured across the filter, due to the filter and any accumulation of solid foreign matter on or in the filter.
Data Length: 1 byte
Resolution: 0.05 kPa/bit gain, 0 kPa offset
Data Range: 0 to +12.5 kPa (0 to +1.8 psi)
Type: Measured
Suspect Parameter Number: 107

5.6 Exhaust Gas Temperature—Temperature of combustion byproducts leaving the engine.
Data Length: 2 bytes
Resolution: 0.03125 °C/bit gain, -273 °C offset
Data Range: -273 to +1735.0 °C (-459.4 to 3155.0 °F)
Type: Measured
Suspect Parameter Number: 173

5.7 Coolant Filter Differential Pressure—Change in coolant pressure, measured across the filter, due to the filter and any accumulation of solid or semisolid matter on or in the filter.
Data Length: 1 byte
Resolution: 0.5 kPa/bit gain, 0 kPa offset
Data Range: 0 to +125 kPa (0 to +18.1 psi) Type: Measured
Suspect Parameter Number: 112

### 6 WATER IN FUEL INDICATOR: WIFL

Transmission repetition rate: | 10 s
Data length: | 8 bytes
Data page: | 0
- X -

Appendix B

PDU format: | 254
PDU specific: | 255
Default priority: | 6
Parameter group number: | 65,279 (00FEFF16)
Byte: 1 Water in fuel indicator | 6.1
2-8 Not defined

6.1 Water In Fuel Indicator—Signal which indicates the presence of water in the fuel.
00- No
01- Yes
Type: Measured
Suspect Parameter Number: 97

### 7 TORQUE/SPEED CONTROL #1: TSC1

Transmission repetition rate: when active; 10 ms to the engine - 50 ms to the retarder
Data length: | 8 bytes
Data page: | 0
PDU format: | 0
PDU specific: | Destination address
Default priority: | 3
Parameter group number: | 0 (00000016)

Byte: 1 Control bits Bit: 8-7 Not defined
6,5 Override control mode priority | 7.1
4,3 Requested speed control conditions | 7.2
2,1 Override control modes | 7.3
2,3 Requested speed/Speed limit | 7.4
4 Requested torque/Torque limit | 7.5
5-8 Not defined

NOTE—Retarder may be disabled by commanding a torque limit of 0%. For example, this permits the brake switch to enable the retarder, up to an amount selected by another device or the operator. Note that the brake switch can be treated as an operator input (mode 00012) or as a brake system input (mode 10102) relative to the active torque mode.

7.1 Override Control Mode Priority (2 bits)—This field is used as an input to the engine or retarder to determine the priority of the Override Control Mode received in the Torque/Speed Control message. The default is 11 (Low priority). It is not required to use the same priority during the entire override function. For example, the transmission can use priority 01 (High priority) during a shift, but can set the priority to 11 (Low priority) at the end of the shift to allow traction control to also interact with the torque limit of the engine.
The four priority levels defined are:
00- Highest priority
- XI -

Appendix B

01- High priority
10- Medium priority
11- Low priority
Type: Status
Suspect Parameter Number: 897

7.1.1 Highest Priority 00—Used for situations that require immediate action by the receiving device in order to provide safe vehicle operation (i.e., braking systems). This level of priority should only be used in safety critical conditions.
7.1.2 High Priority 01—Used for control situations that require prompt action in order to provide safe vehicle operation. An example is when the transmission is performing a shift and requires control of the engine in order to control driveline reengagement.
7.1.3 Medium Priority 10—Used for powertrain control operations which are related to assuring that the vehicle is in a stable operating condition. An example is when the traction control system is commanding the engine in order to achieve traction stability.
7.1.4 Low Priority 11—Used to indicate that the associated command desires powertrain control but is needed for function which improves the driver comfort which may be overridden by other devices. An example is cruise control or the non-critical part of a transmission shift to a new gear.

7.2 Requested Speed Control Conditions (2 bits)—This mode tells the engine control system the governor characteristics that are desired during speed control. The four characteristics defined are: 00 - Transient Optimized for driveline disengaged and non-lockup conditions 01 - Stability Optimized for driveline disengaged and non-lockup conditions 10 - Stability Optimized for driveline engaged and/or in lockup condition 1 (e.g., vehicle driveline) 11 - Stability Optimized for driveline engaged and/or in lockup condition 2 (e.g., PTO driveline) Type: Status Suspect Parameter Number:696

- XII -

Appendix B

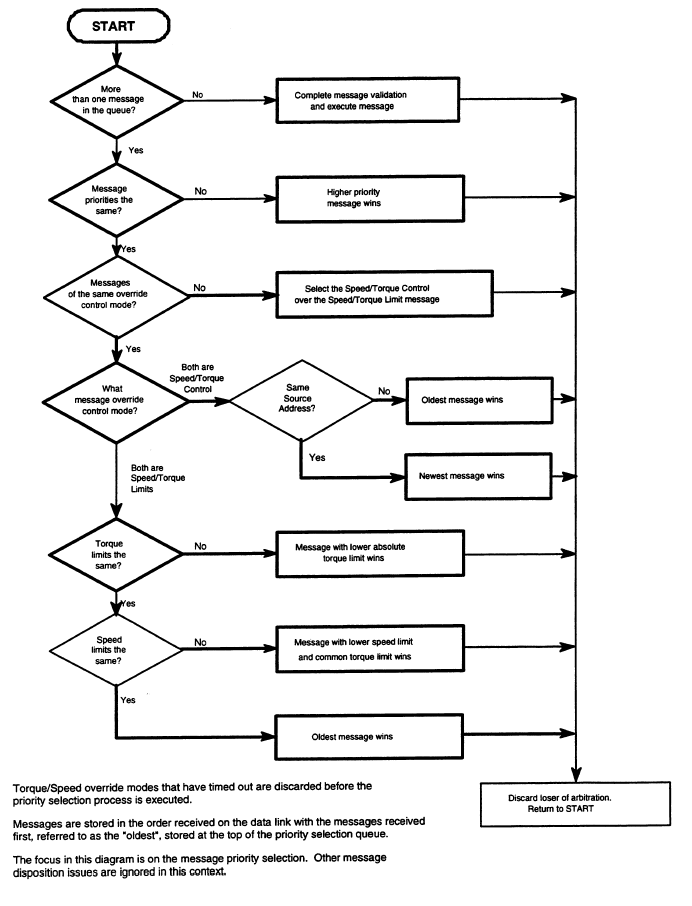
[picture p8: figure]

Figure 3 - Torque/Speed control priority selection logic

7.2.1 Speed Control Characteristic 00—This speed governor gain selection is adjusted to provide rapid transition between speed setpoints. RPM overshoot and undershoot may be greater than what is seen when the “speed control characteristic” is set to be stability optimized.
7.2.2 Speed Control Characteristic 01—This control condition has been optimized to minimize rpm overshoot and undershoot given an expected plant consisting of the engine and its accessory loads. This gain adjustment is not intended to compensate for driveline characteristics. This characteristic is most appropriate when no driveline is connected.
- XIII -

Appendix B

7.2.3 Speed Control Characteristic 10—This control condition has been optimized to minimize rpm overshoot and undershoot given a more complex plant. For instance, the more complex plant would contain the engine, its accessory loads and the driveline characteristics. As an example the driveline characteristics might include the effective spring mass relationship of pumps, tires, clutches, axles, driveshafts, and multiple gear ratios. This characteristic is most appropriate when a driveline is engaged.
7.2.4 Speed Control Characteristic 11—This speed control characteristic is available for applications requiring compensation for more than one driveline characteristic. It has been optimized to minimize rpm overshoot and undershoot given a more complex plant of the second variety. This more complex plant would again contain the engine, its accessory loads and a second driveline characteristic unique from the one described in speed control characteristic 10.
7.3 | Override Control Mode (2 bits)—The override control mode defines which sort of command is used: 00 - Override disabled - Disable any existing control commanded by the source of this command. 01 - Speed control - Govern speed to the included “desired speed” value. 10 - Torque control - Control torque to the included “desired torque” value. 11 - Speed/torque limit control - Limit speed and/or torque based on the included limit values. The speed limit governor is a droop governor where the speed limit value defines the speed at the maximum torque available during this operation. Type: Status Suspect Parameter Number:695
| If a device wants to know whether it has access to the engine, there are several possibilities:
a. Comparing its command with the actual engine broadcasts.
b. Looking at command modes from other devices.
c. Looking to the engine and retarder torque mode.
| Remarks:
a. The realization of a torque limit (minimum selection) is possible by setting
| the speed limit to a high value (FAFF16).
b. The realization of a speed limit (minimum selection) is possible by setting
| the torque limit to a high value (FA16).
c. Limiting the retarder torque means to limit the magnitude of the torque
| request. As the brake torque is represented by negative torque values, the limitation must be done by a maximum selection of the requested torque and the retarder internal torque signals.
d. For torque increasing functions, time limits for the torque or speed value
| (command) and the direct modes are desirable.
e. The selection of which device has control of the engine's speed or torque
| depends on the override mode priority (see 7.1) with the highest priority device gaining control. In the case of two devices with identical priority, the engine responds to speed/torque control commands over speed/torque limit commands and will act on the speed or torque commands on a first
- XIV -

Appendix B

come, first served basis. The torque limit will be a “lowest wins” selection (e.g, if one device commands 60% limit and another 80% limit, then the engine will limit torque to 60%). Figure 3 provides a flowchart of the torque/speed control priority selection logic.

7.4 | Requested Speed—Parameter provided to the engine from external sources in the torque/speed control message. This is the engine speed which the engine is expected to operate at if the speed control mode is active or the engine speed which the engine is not expected to exceed if the speed limit mode is active. Data Length: 2 bytes Resolution: 0.125 rpm/bit gain, 0 rpm offset (upper byte resolution = 32 rpm/bit) Data Range: 0 to 8031.875 rpm Type: Status Suspect Parameter Number: 898
7.5 | Requested Torque—Parameter provided to the engine or retarder in the torque/speed control message for controlling or limiting the output torque. Requested torque to the engine is measured in indicated torque as a percentage of peak engine torque. This is the engine torque at which the engine is expected to operate if the torque control mode is active or the engine torque which the engine is not expected to exceed in the torque limit mode is active. Zero torque can be requested which implies zero fuel and, according to

Figures 1 and 2, the engine will not be allowed to stall. The actual engine
| percent torque (2.3) should be zero and the engine should decelerate until the low idle governor kicks in, at which time the actual engine percent torque will be calculated as shown in Figures 1 and 2 and the engine torque mode bits
(2.1) should be equal to 00002 - Low Idle Governor.
| Requested torque to the retarder is measured in indicated torque as a percentage of peak retarder torque. The logic used in enabling or disabling the retarder is based on the override control mode priority bits (7.1). Data Length: 1 byte Resolution: 1%/bit gain, -125% offset Data Range: -125 to 125% Operating range: 0 to 125% for engine torque requests -125 to 0% for retarder torque requests Type: Status Suspect Parameter Number: 518
| The driver input in Table 2 refers to the enable retarder - brake assist switch (4.2.2.11 in standard document). The driver input switch should not power the retarder control directly, otherwise it is not possible for other devices on the network to request retardation and override the driver. Engine retarders cannot be activated while the engine is being fuelled. During simultaneous network commands for both retarder enable and engine speed or torque control, the retarder commands will be restricted if the engine is not zero brake torque, and allowed once the engine achieves zero brake torque. During Electronically Controlled Braking, where the brake pedal position (or pressure) directly relates to the amount or retardation, the driver preselected level is not used to
- XV -

Appendix B

determine the amount of retardation provided by the engine brake.
A separate enable retarder - shift assist switch (4.2.2.12 in standard document) is used by the transmission to decide if network control should be used to activate the engine retarder for shift assist. When this switch is enabled, the transmission may use network commands to activate the engine retarder in order to enhance engine decel rates and improve shift control.
The retarder is available for cruise control only if the retarder is first enabled by the driver using the brake assist switch.

The “previous state” when all devices become “don't care” may depend on an earlier set of conditions (i.e., a device may request retardation temporarily and then “don't care.” The retarder should then return to its “previous state.” This is typically zero retardation, but not in all cases).
Multiple retarder control messages from the network are handled through the use of the override control mode priority bits described in 7.1.

Table 2 - Primary retarder - Before transmission (Engine Retarder)

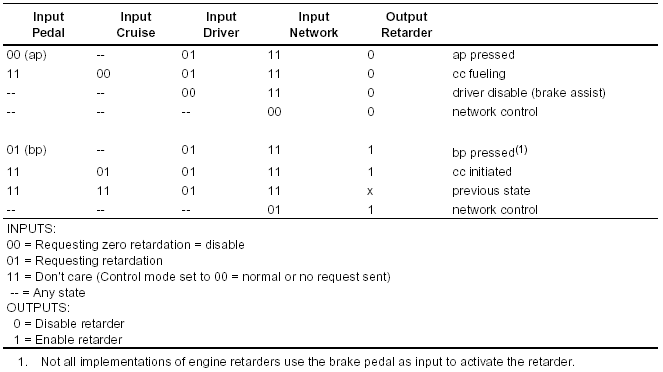
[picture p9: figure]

The driver input in Table 3 refers to the switch setting (i.e., off, percent on). The driver select switch should not power the retarder control directly, otherwise it is not possible for other devices on the network to request retardation and override the driver.
The retarder is available for cruise control only if the retarder is first enabled by the driver.
The “previous state” when all devices become “don't care” may depend on an earlier set of conditions (i.e., a device may request retardation temporarily and then “don't care.” The retarder should then return to its “previous state.” This is typically zero retardation, but not in all cases).
Multiple retarder control messages from the network are handled through the use of the override control mode priority bits described in 7.1.
- XVI -

Appendix B

Table 3 - Primary retarder - Before transmission (Exhaust Brake)

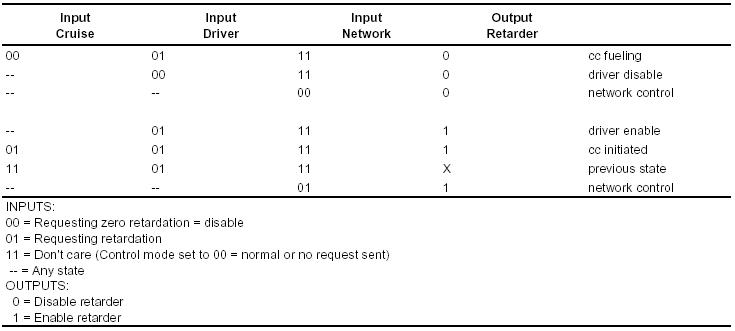
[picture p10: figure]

The driver input in Table 4 refers to the selector switch setting of the retarder (e.g., off, 20%, 40%, 50%, 80%, 100%). During Electronically Controlled Braking, where the brake pedal position (or pressure) directly relates to the amount or retardation, the driver preselected level is not used to determine the amount of retardation. Also note that cruise control or the driver can independently disable the retarder, but that the cruise control can only override the driver select switch to use the retarder if the driver selector switch is not off.
Multiple retarder control messages from the network are handled through the use of the override control mode priority bits described in 7.1

Table 4 - Secondary retarder - After transmission (Transmission/Driveline Retarders)

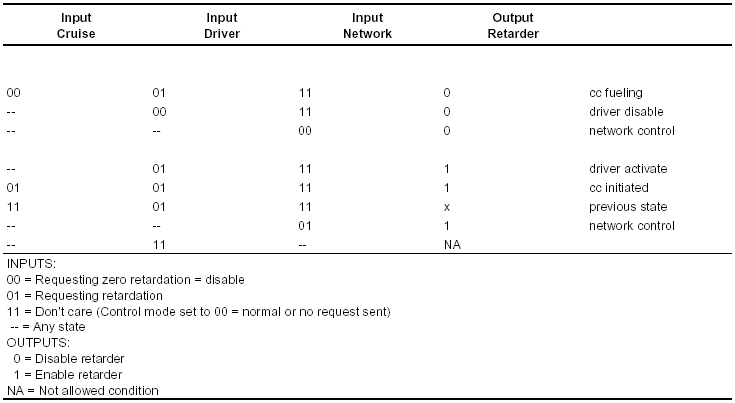
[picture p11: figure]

- XVII -

Appendix B

## Extract from standard document SAE J1939/21

SAE International SAE J1939/21, Surface Vehicle Recommended Practice – Data Link Layer, Issued 1994-07, Revised 1998-07

Messages from standard SAE J1939

### 8 Broadcast Announce Message (BAM)

The TP.CM_BAM is used to inform all the nodes of the network that a large message is about to be broadcast. It defines the parameter group and the number of bytes to be sent. After TP.CM_BAM is sent, the Data Transfer Messages are sent and they contain the packetized broadcast data.
TP.CM_BAM is only transmitted by the originator.
- XVIII -

Appendix C

## Overview of the software

## Blockdiagram of analyse program

## Settings

Channel and Language

## CanBusRead

Reading from CAN

## View Settings

Set message to view

## About

About program

## CanBusDiagnosticTool for PocketPC

- I -

Appendix C

## Blockdiagram with GUI screenshots

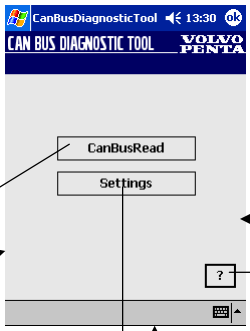
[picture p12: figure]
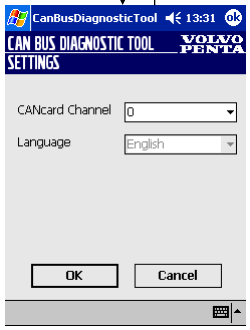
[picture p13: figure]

- II -

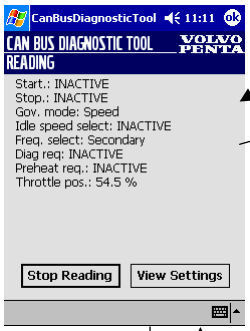
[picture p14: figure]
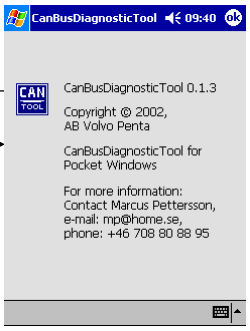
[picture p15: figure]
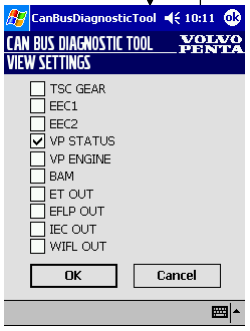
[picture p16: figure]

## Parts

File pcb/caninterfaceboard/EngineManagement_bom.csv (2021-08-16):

Source | /Users/ieb/timefields/PlatformIO/Projects/EngineManagement/pcb/EngineManagement.sch
Kicad Rev | Eeschema 4.0.6
Generated Date | Monday | 09 August 2021 'pmt' 14:41:13
Title | Not Set
Company | Not Set
Revision | Not Set
Date Issue | Not Set
[x] P5 | LCD | conn | CONN_4 | Headers from stock | Order EBAY 4x20 i2c
[ ] U2 | DPDTRelay | 1966260 | device | DPDTRelay | Order RS
[ ] U6 | MCP23008 | device | MCP23008 | Oder RS
[ ] R25 | 1M | device | R | Order RS
[x] Deutch 6 way plug ordered EBAy
[x] Deutch 6 way plug Stock
[x] Deutch 8 way plug ordered EBAy
[ ] Box (space available for 130*225 or 245 at a crush)
[ ] Wire
[X] 4 12v relays stock.
[X] 10A 1KV diodes | ebay
Reference | Value | RS Number | Library | Library Ref
F1 | FUSE 5A | device | FUSE | Crmp Holders
D1 | SMBJ30CA-TR TSV | device | DIODE | On boat or RS
P1 | Buttons | conn | CONN_6 | 2xway from stock
U3 | ArdinoMinPro | device | ArdinoMinPro | from stock
R19 | 10K | device | R | from stock
R23 | 1K | device | R | from stock
R22 | 100K | device | R | from stock
C4 | 10nF | device | C | from stock
R24 | 1K | device | R | from stock
R21 | 100K | device | R | from stock
C5 | 10nF | device | C | from stock
R25 | 1M | device | R | Order EBAY
R26 | 470K | device | R | from stock
C6 | 1nF | device | C | from stock
R27 | 1M | device | R | Order EBAY
R28 | 470K | device | R | from stock
C7 | 1nF | device | C | from stock
R29 | 1M | device | R | Order EBAY
R30 | 470K | device | R | from stock
C8 | 1nF | device | C | from stock
R31 | 1M | device | R | Order EBAY
R32 | 470K | device | R | from stock
C9 | 1nF | device | C | from stock
U1 | LM7808CT | regul | LM7808CT | from stock
C2 | 100uF | device | CAPAPOL | from stock
C3 | 10nF | device | C | from stock
D3 | 1N5819 | device | DIODE | from stock
R9 | 10R | device | R | from stock
P5 | LCD | conn | CONN_4 | Headers from stock | Order EBAY 4x20 i2c
U4 | RS485 | device | RS485 | from stock
K2 | RS485 | conn | CONN_3 | from stock
U5 | MCP2515Shield | device | MCP2515Shield | from stock
P6 | J1939 | conn | CONN_4 | from stock
K5 | FuelCool | conn | CONN_3 | from stock
K7 | FlyOil | conn | CONN_3 | from stock
K6 | AltBatt | conn | CONN_3 | from stock
F2 | FUSE 40A | device | FUSE | from stock
D2 | SMBJ30CA-TR TSV | device | DIODE | from stock
C1 | 10nF | device | C | from stock
C10 | 10nF | device | C | from stock
R3 | 47K | device | R | from stock
R4 | 47K | device | R | from stock
D6 | 1N5819 | device | DIODE | from stock
D5 | 1N5819 | device | DIODE | from stock
U6 | MCP23008 | device | MCP23008 | Oder Ebay
RL1 | EnginePower | power | AutomotiveRelay | from stock
RL2 | EngineStart | power | AutomotiveRelay | from stock
RL3 | EngineStop | power | AutomotiveRelay | from stock
RL4 | GlowPlugs | power | AutomotiveRelay | from stock
U8 | 8WayRelayBoard | device | 8WayRelayBoard | from stock
U2 | DPDTRelay | 1966260 | device | DPDTRelay | Order RS
R2 | 10K | device | R | from stock
R1 | 2.2K | device | R | from stock
D4 | 1N5819 | device | DIODE | from stock
U7 | LM7805CT | regul | LM7808CT | from stock
C11 | 10nF | device | C | from stock
R5 | 10K | device | R | from stock
P2 | CONN_1 | conn | CONN_1 | from stock
P3 | CONN_1 | conn | CONN_1 | from stock
P4 | CONN_1 | conn | CONN_1 | from stock
R10 | 10K | device | R | from stock
R8 | 10K | device | R | from stock
R7 | 10K | device | R | from stock
R6 | 10K | device | R | from stock
R12 | 10K | device | R | from stock
R11 | 10K | device | R | from stock
R14 | 10K | device | R | from stock
R13 | 10K | device | R | from stock
Q1 | 2N2907 | device | PNP | from stock
K1 | SwitchedPower | conn | CONN_3 | from stock
P7 | RelayBoard | conn | CONN_10 | from stock

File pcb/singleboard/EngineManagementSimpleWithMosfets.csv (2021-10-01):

Source | /Users/ieb/timefields/PlatformIO/Projects/EngineManagement/pcb/EngineManagementSimpleWithMosfets.sch
Kicad Rev | Eeschema 4.0.6
Generated Date | Monday | 27 September 2021 'pmt' 12:06:12
Title | Not Set
Company | Not Set
Revision | Not Set
Date Issue | Not Set
Reference | Value | Library | Library Ref
F1 | FUSE 5A | device | FUSE
D1 | SMBJ30CA-TR TSV | device | DIODE
F2 | FUSE 30A | device | FUSE
D7 | 5A 600V | device | DIODE
D10 | 10A 600V | device | DIODE
D8 | 10A 600V | device | DIODE
D9 | 1A 40V | device | DIODE
R7 | 10R | device | R
F3 | 6A Breaker | device | FUSE
F4 | 6A breaker | device | FUSE
F5 | 6A breaker | device | FUSE
SW2 | Start | device | SW_PUSH
SW3 | Stop | device | SW_PUSH
SW4 | Glow | device | SW_PUSH
U2 | Tachometer | device | Tachometer
U3 | WaterTemp | device | Tachometer
R11 | 1K | device | R
D2 | ChargeWarn | device | LED
D5 | OilWarn | device | LED
R19 | 1K | device | R
U1 | LM358 | linear | LM358
R2 | 330R | device | R
Q5 | 2N2907 | device | PNP
Q6 | 2N2907 | device | PNP
R18 | 2.2K | device | R
R21 | 10K | device | R
R20 | 2.2K | device | R
R17 | 10K | device | R
R5 | 10K | device | R
SP1 | Buzzer | device | SPEAKER
D4 | TempWarn | device | LED
R16 | 1K | device | R
R4 | 10K | device | R
R12 | 10M | device | R
C2 | 10uF | device | CAPAPOL
C1 | 10nF | device | C
P10 | VP ButtonPlug | conn | CONN_6
P9 | VP MultiLinkPlug | conn | CONN_6
P8 | VP EnginePlug | conn | CONN_8
D3 | 10A100V | device | DIODE
Q1 | 2N2907 | device | PNP
R3 | 10K | device | R
R6 | 2.2K | device | R
SW1 | ON/OFF | device | SW_PUSH
R22 | 1K | device | R
F7 | FUSE 15A | device | FUSE
F6 | FUSE 40A | device | FUSE
D14 | OilWarn | device | LED
R23 | 1K | device | R
P1 | VPButtons | conn | CONN_5
P5 | 12VSwitchedPower | conn | CONN_1
P3 | StarterSolenoidT30 | conn | CONN_1
P4 | StopSolenoid | conn | CONN_1
P2 | ToEngine | conn | CONN_6
RV1 | 20K | device | POT
P6 | GlowPlugs | conn | CONN_1
Q3 | SI7137 | device | MOSFET_P
Q9 | SI7137 | device | MOSFET_P
Q4 | SI7137 | device | MOSFET_P
Q7 | SI7137 | device | MOSFET_P
D18 | 5A 600V | device | DIODE
D13 | SMBJ30CA-TR TSV | device | DIODE
D6 | SMBJ30CA-TR TSV | device | DIODE
D11 | SMBJ30CA-TR TSV | device | DIODE
R26 | 1K | device | R
R13 | 1K | device | R
R15 | 100R | device | R
R24 | 100R | device | R
R14 | 1K | device | R
Q8 | SI7137 | device | MOSFET_P
R10 | 220R | device | R
R9 | 10K | device | R
R1 | 100R | device | R
R8 | 10K | device | R
D12 | ZENER | device | ZENER
D17 | 10V Zeener | device | ZENER
D15 | ZENER | device | ZENER
D16 | ZENER | device | ZENER
SW5 | Neutral | device | SPST
U5 | Max16054 | device | Max16054
U4 | NCP1117ST50T3G | regul | NCP1117ST50T3G
TH1 | THERMISTOR | device | THERMISTOR
Q2 | BS170 | device | MOS_N
C3 | 10uF | device | CAPAPOL
Q11 | BS250P | device | MOSFET_P
R25 | 10K | device | R
R33 | 220R | device | R
Q15 | BS250P | device | MOSFET_P
R35 | 220R | device | R
R27 | 2.2K | device | R
F8 | FUSE 40A | device | FUSE
D19 | SMBJ30CA-TR TSV | device | DIODE
R28 | 2.2K | device | R
R31 | 100R | device | R
Q13 | BS250P | device | MOSFET_P
R34 | 220R | device | R
D22 | 1N4001 | device | DIODE
D23 | 1N4001 | device | DIODE
D21 | 1N4001 | device | DIODE
D20 | 1N4001 | device | DIODE

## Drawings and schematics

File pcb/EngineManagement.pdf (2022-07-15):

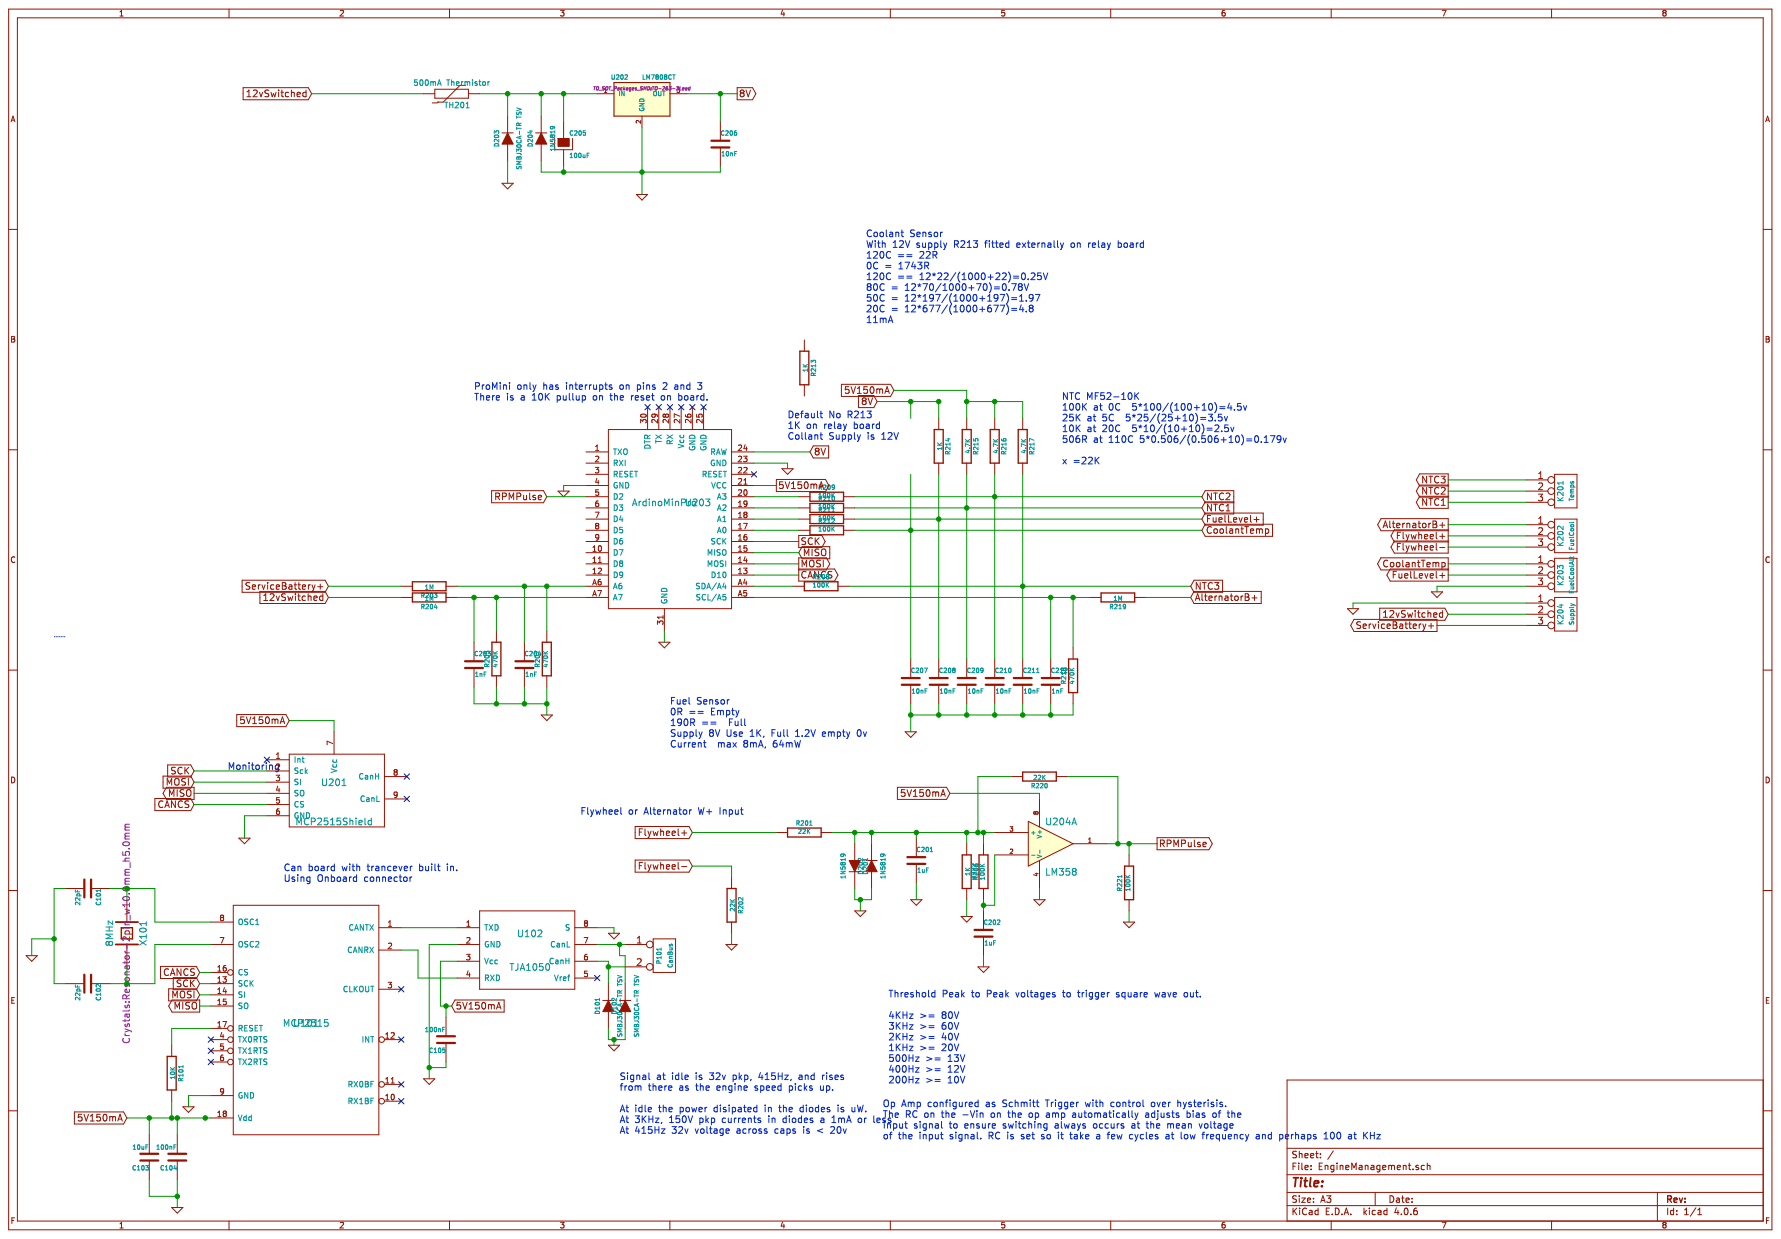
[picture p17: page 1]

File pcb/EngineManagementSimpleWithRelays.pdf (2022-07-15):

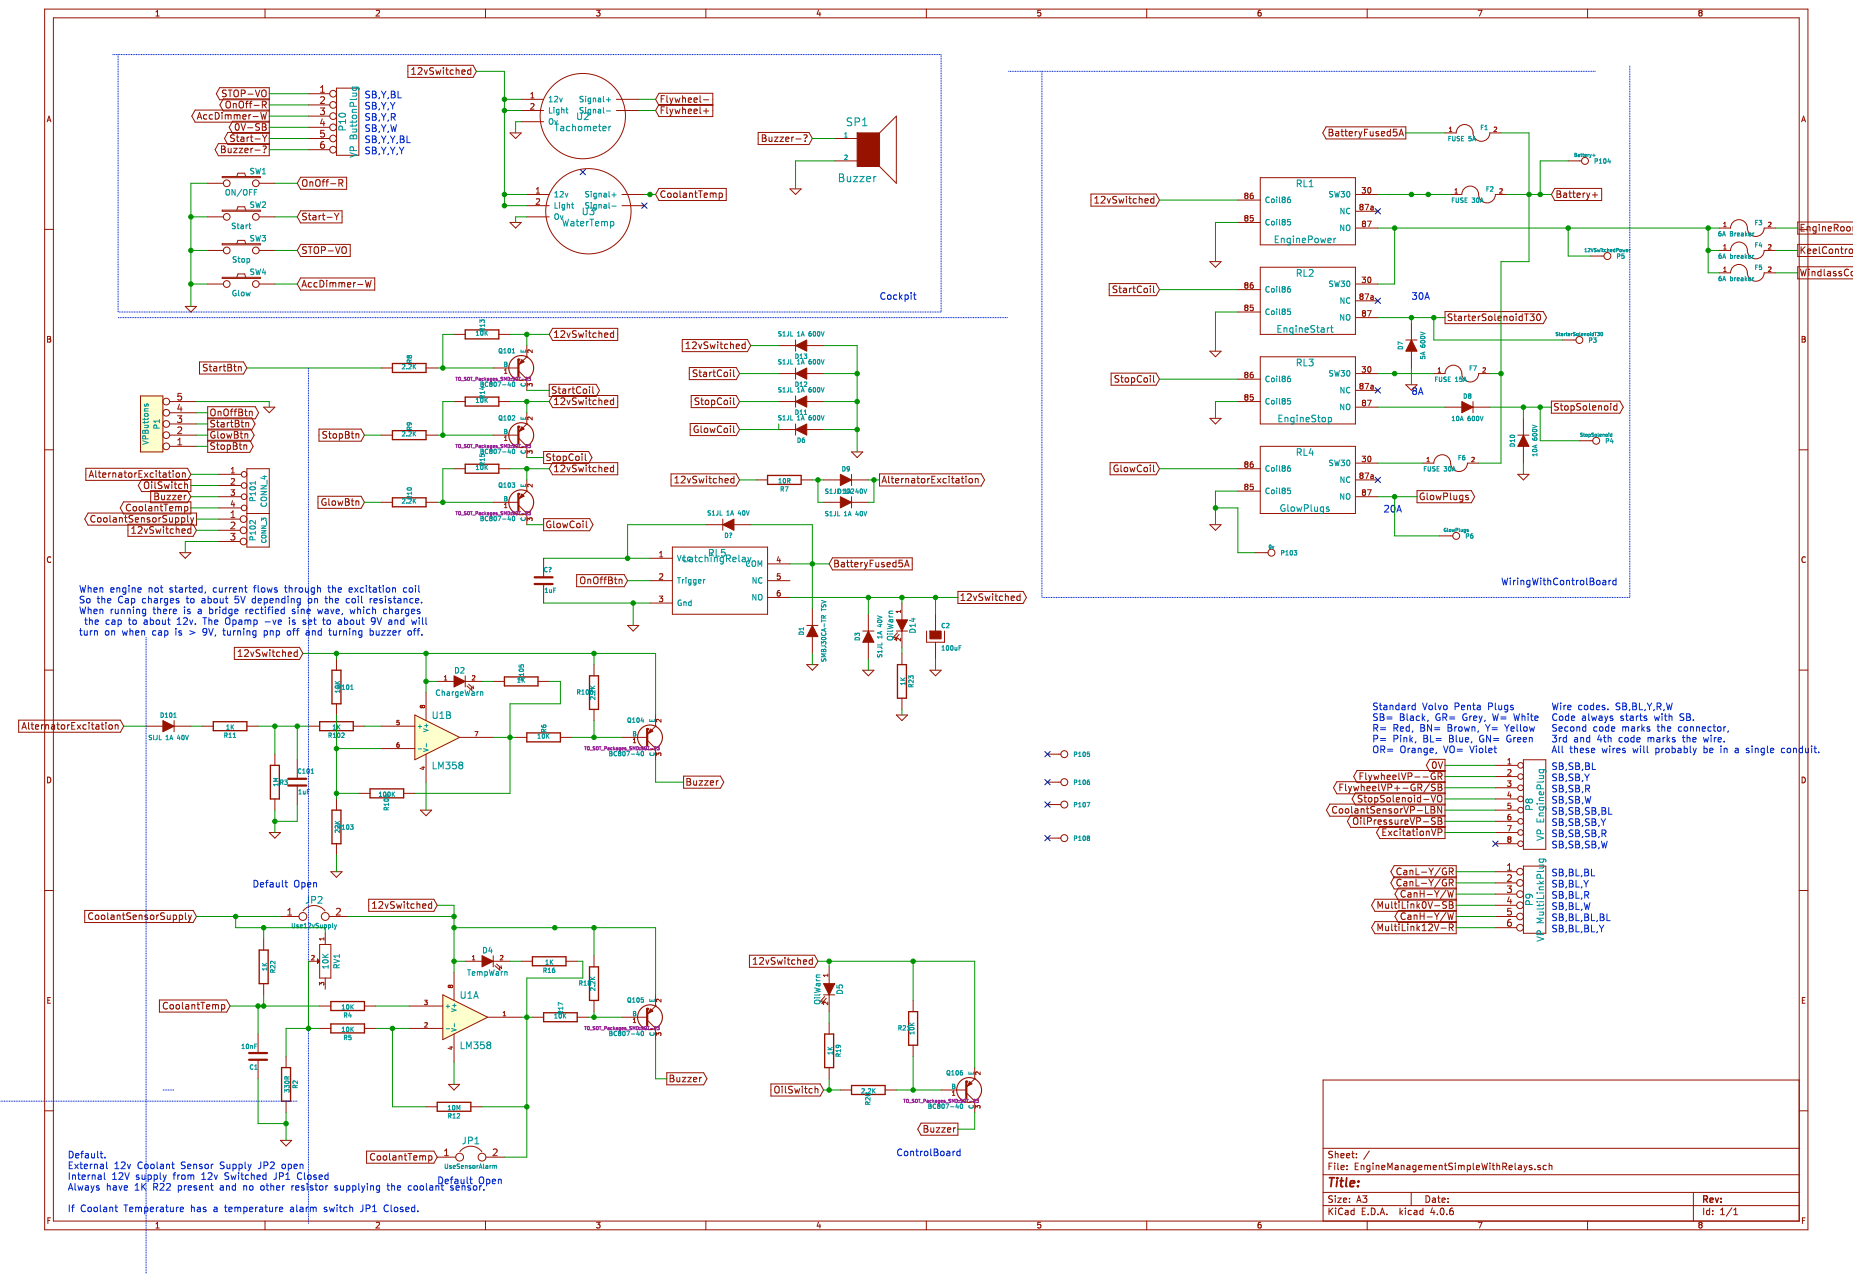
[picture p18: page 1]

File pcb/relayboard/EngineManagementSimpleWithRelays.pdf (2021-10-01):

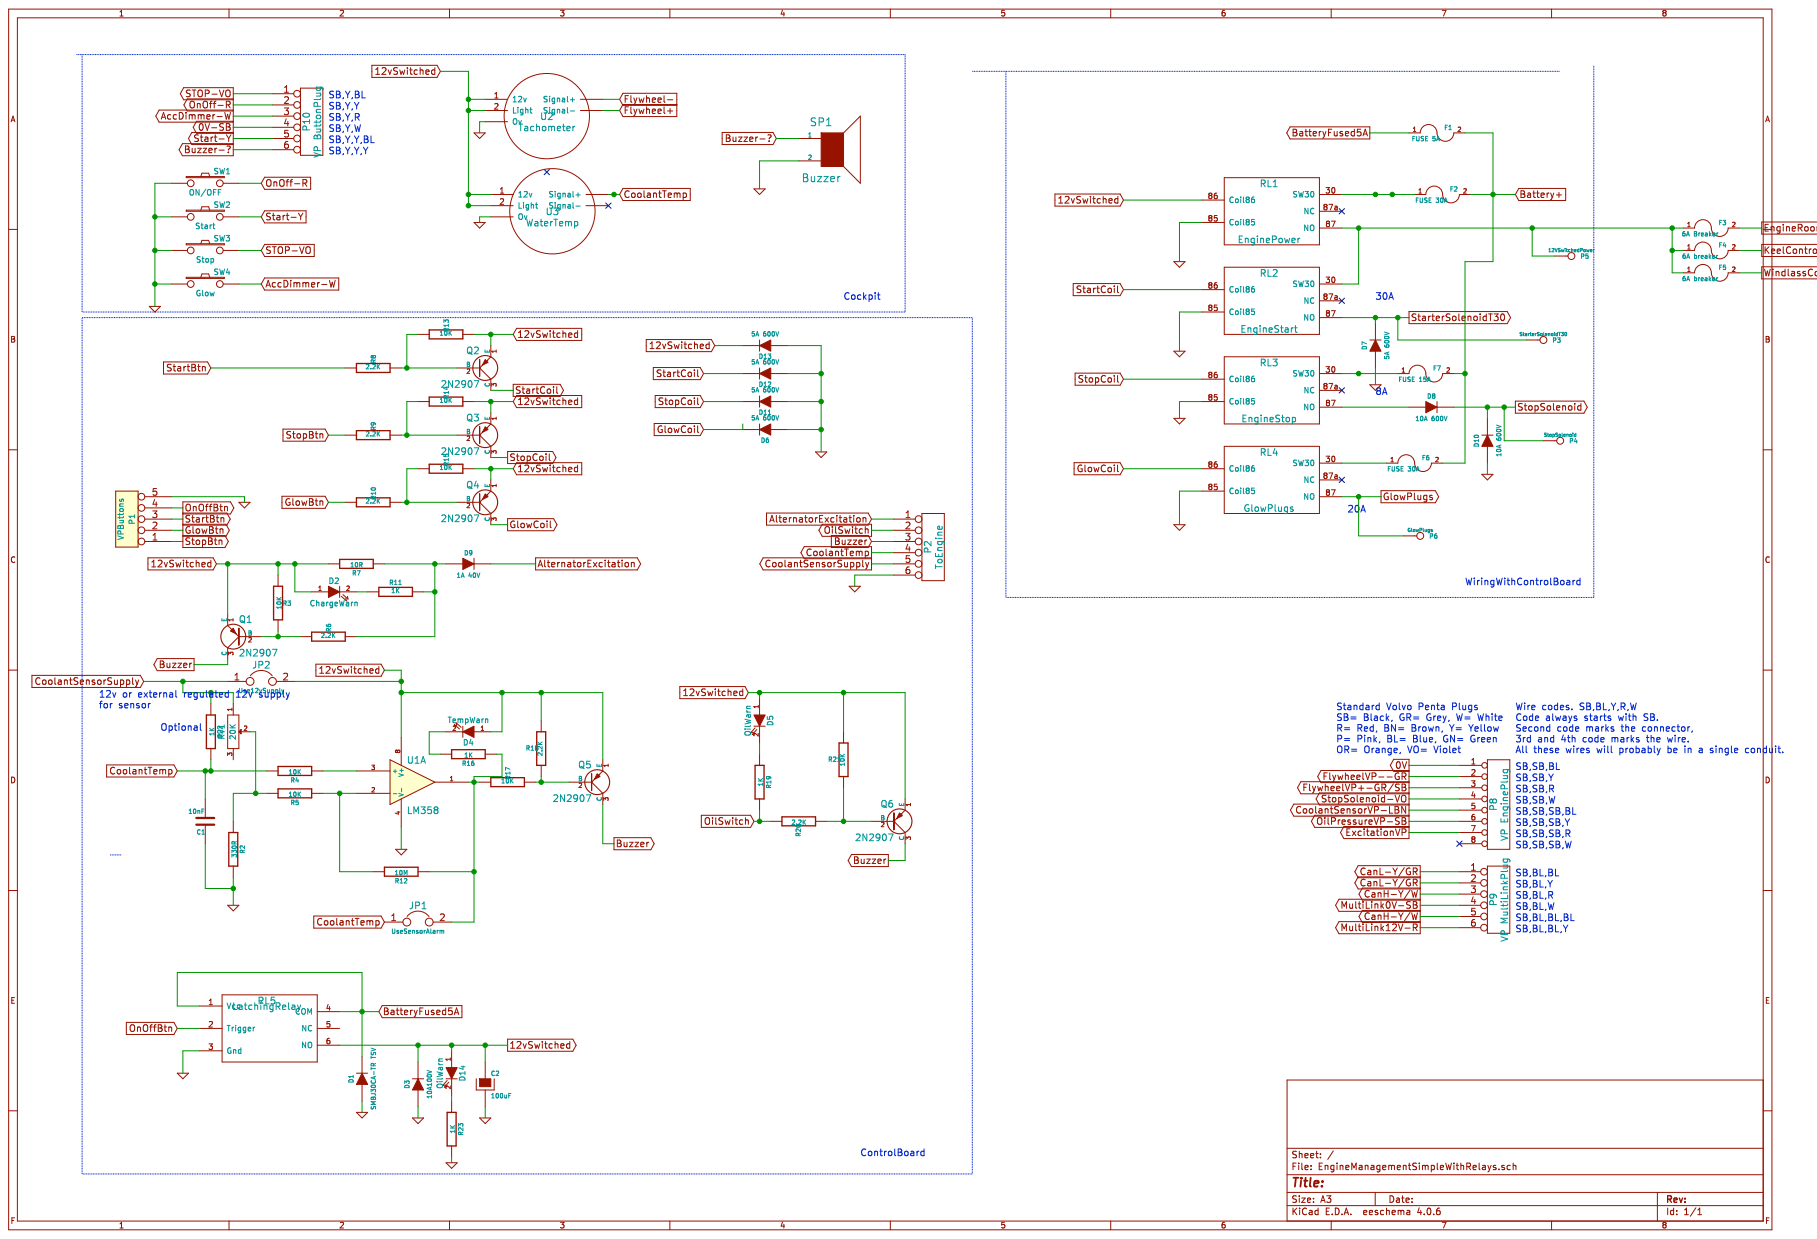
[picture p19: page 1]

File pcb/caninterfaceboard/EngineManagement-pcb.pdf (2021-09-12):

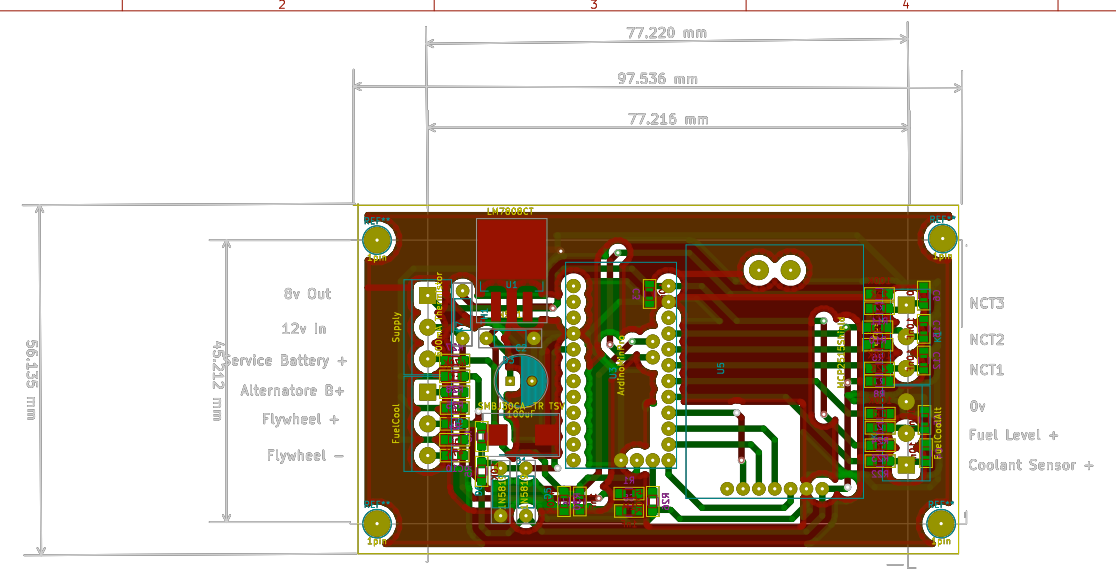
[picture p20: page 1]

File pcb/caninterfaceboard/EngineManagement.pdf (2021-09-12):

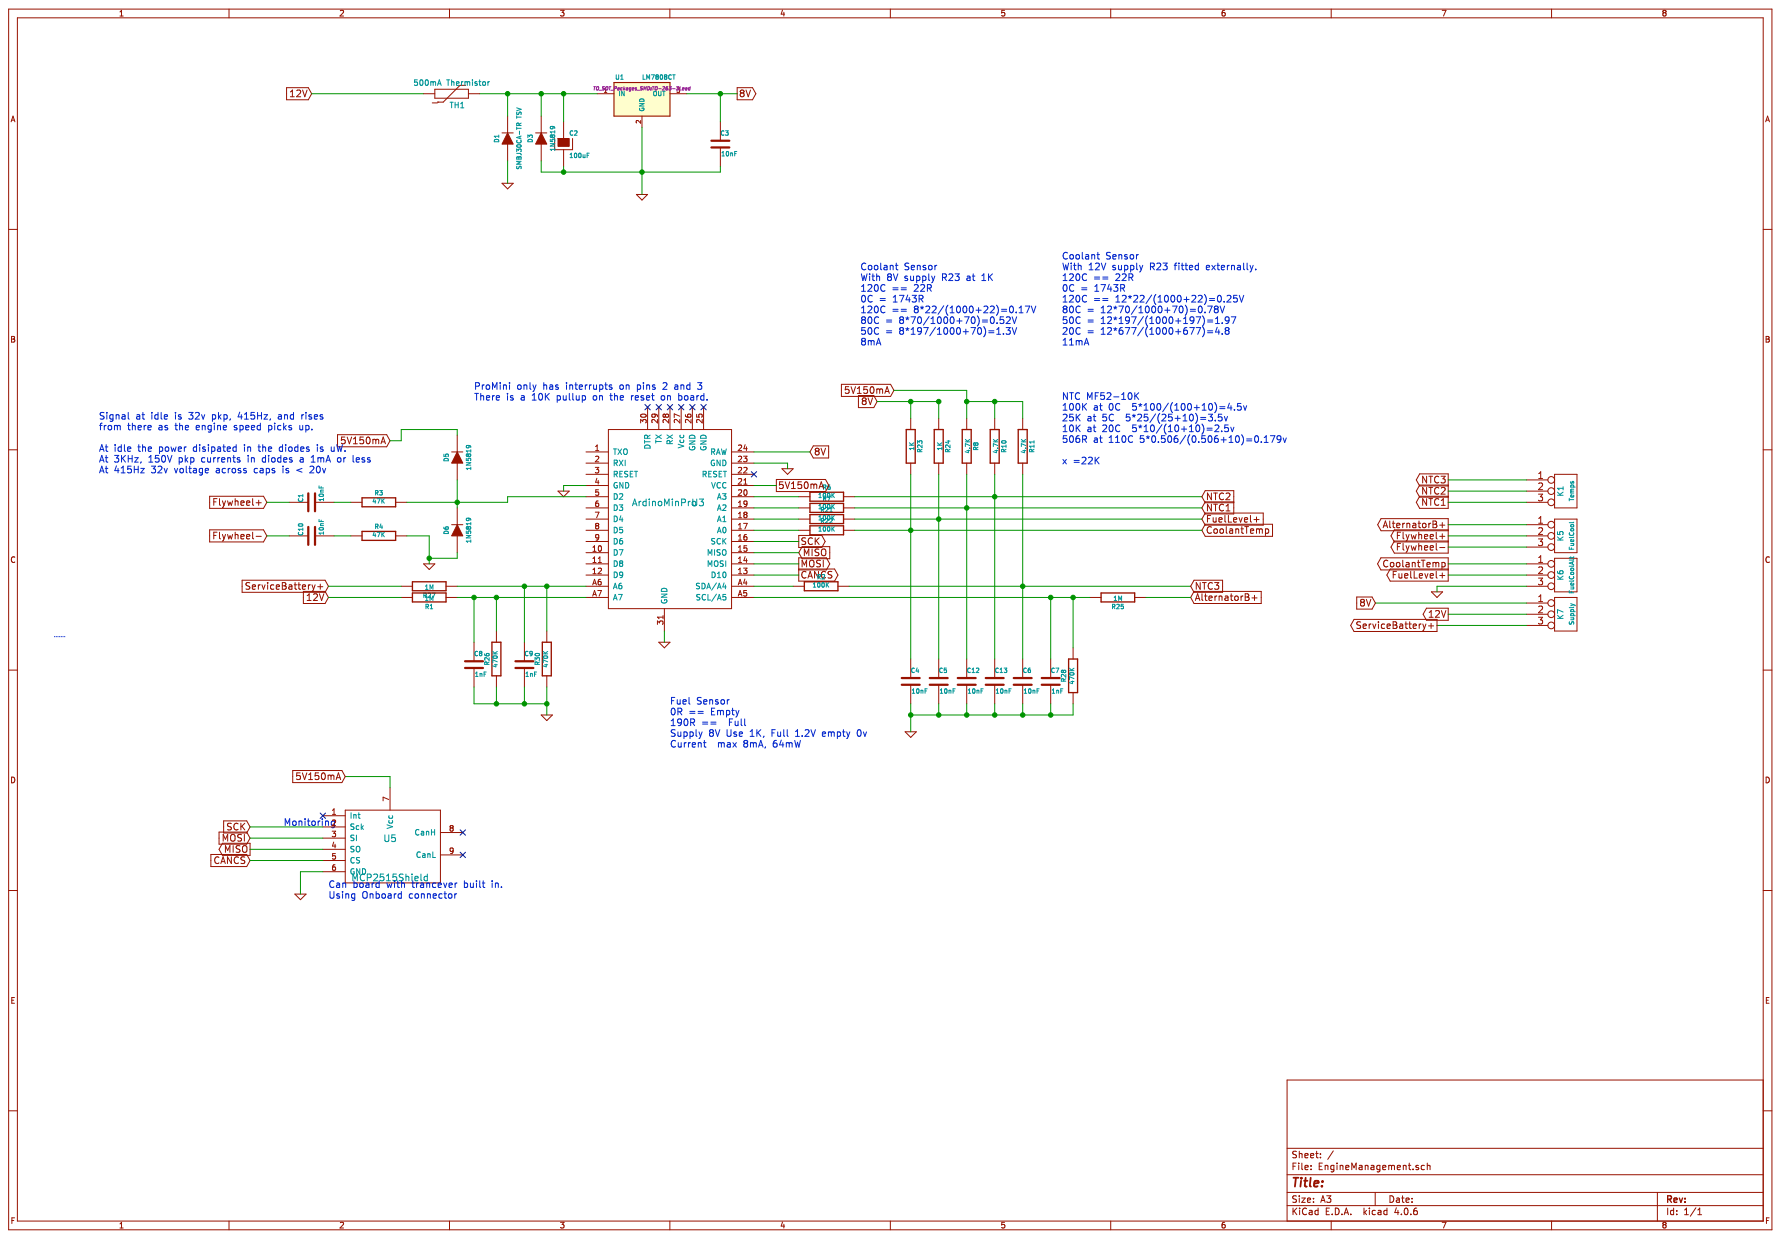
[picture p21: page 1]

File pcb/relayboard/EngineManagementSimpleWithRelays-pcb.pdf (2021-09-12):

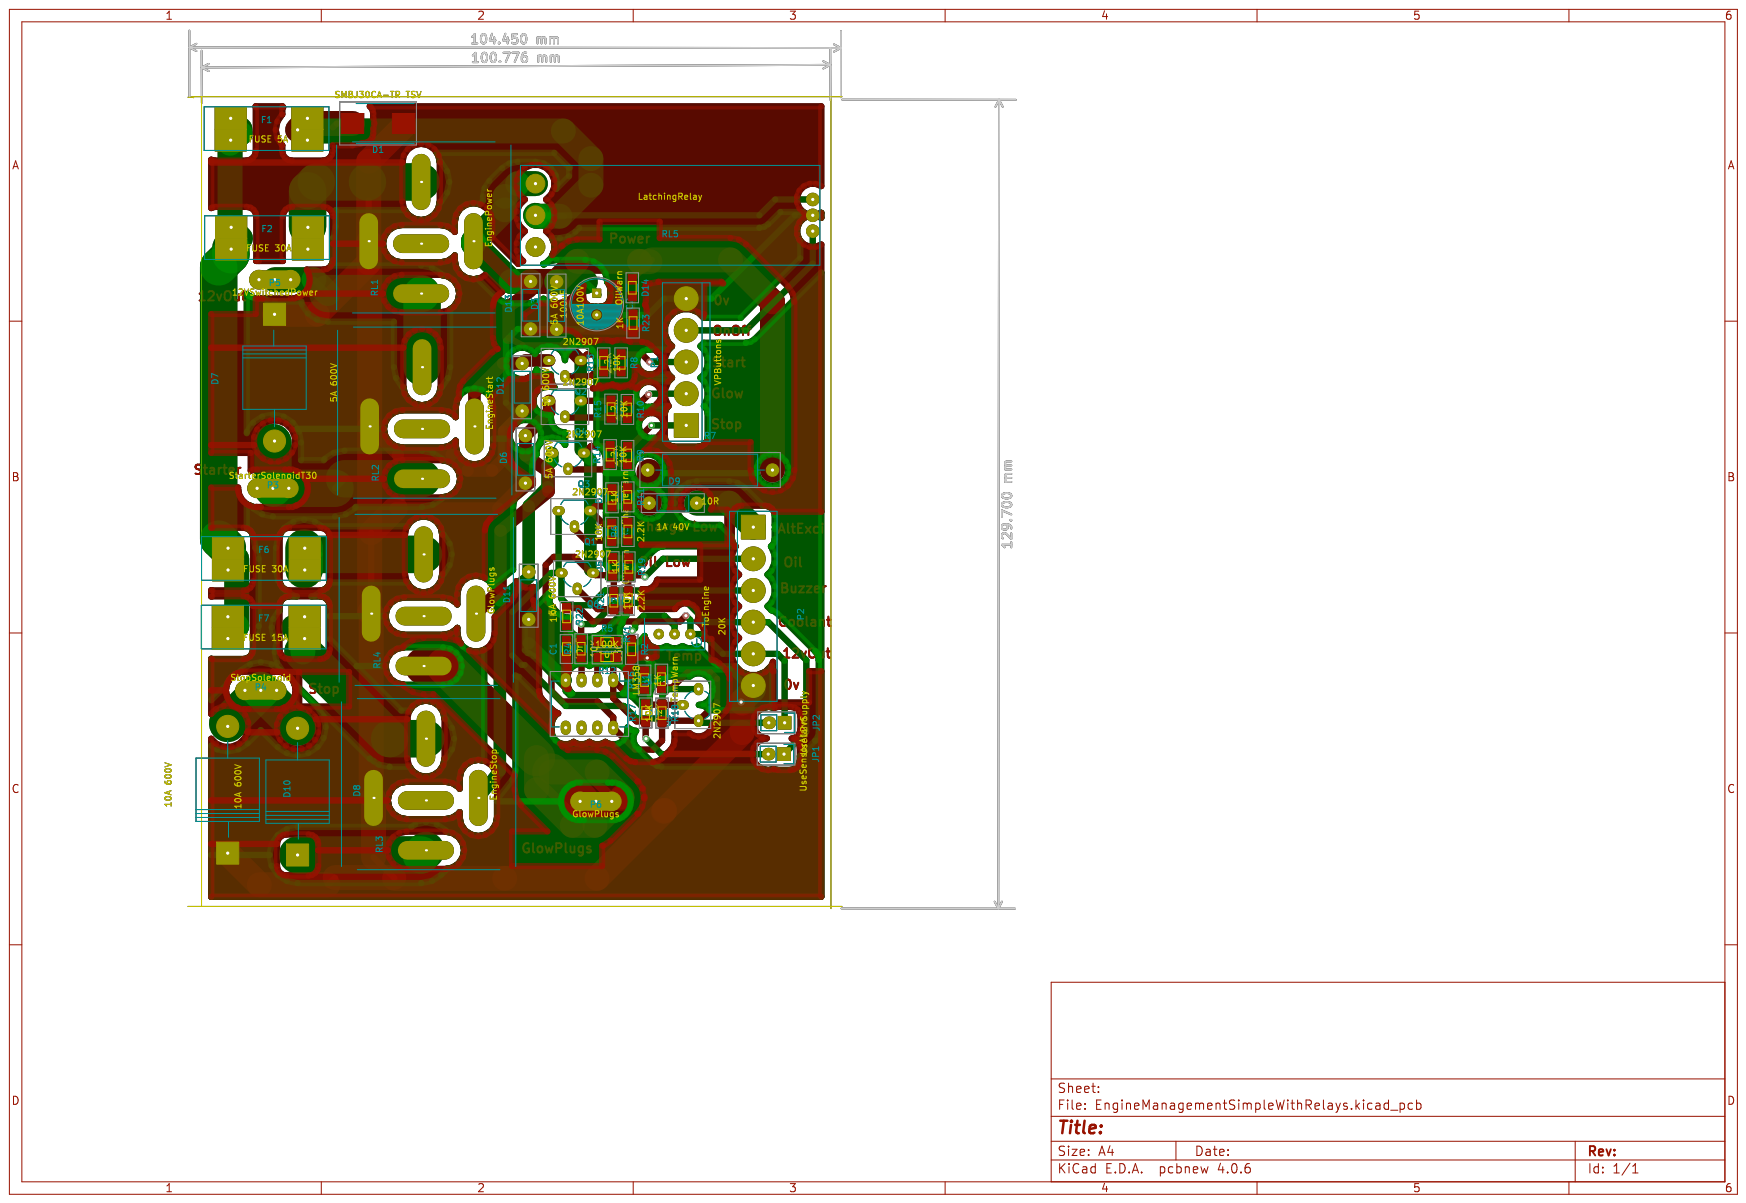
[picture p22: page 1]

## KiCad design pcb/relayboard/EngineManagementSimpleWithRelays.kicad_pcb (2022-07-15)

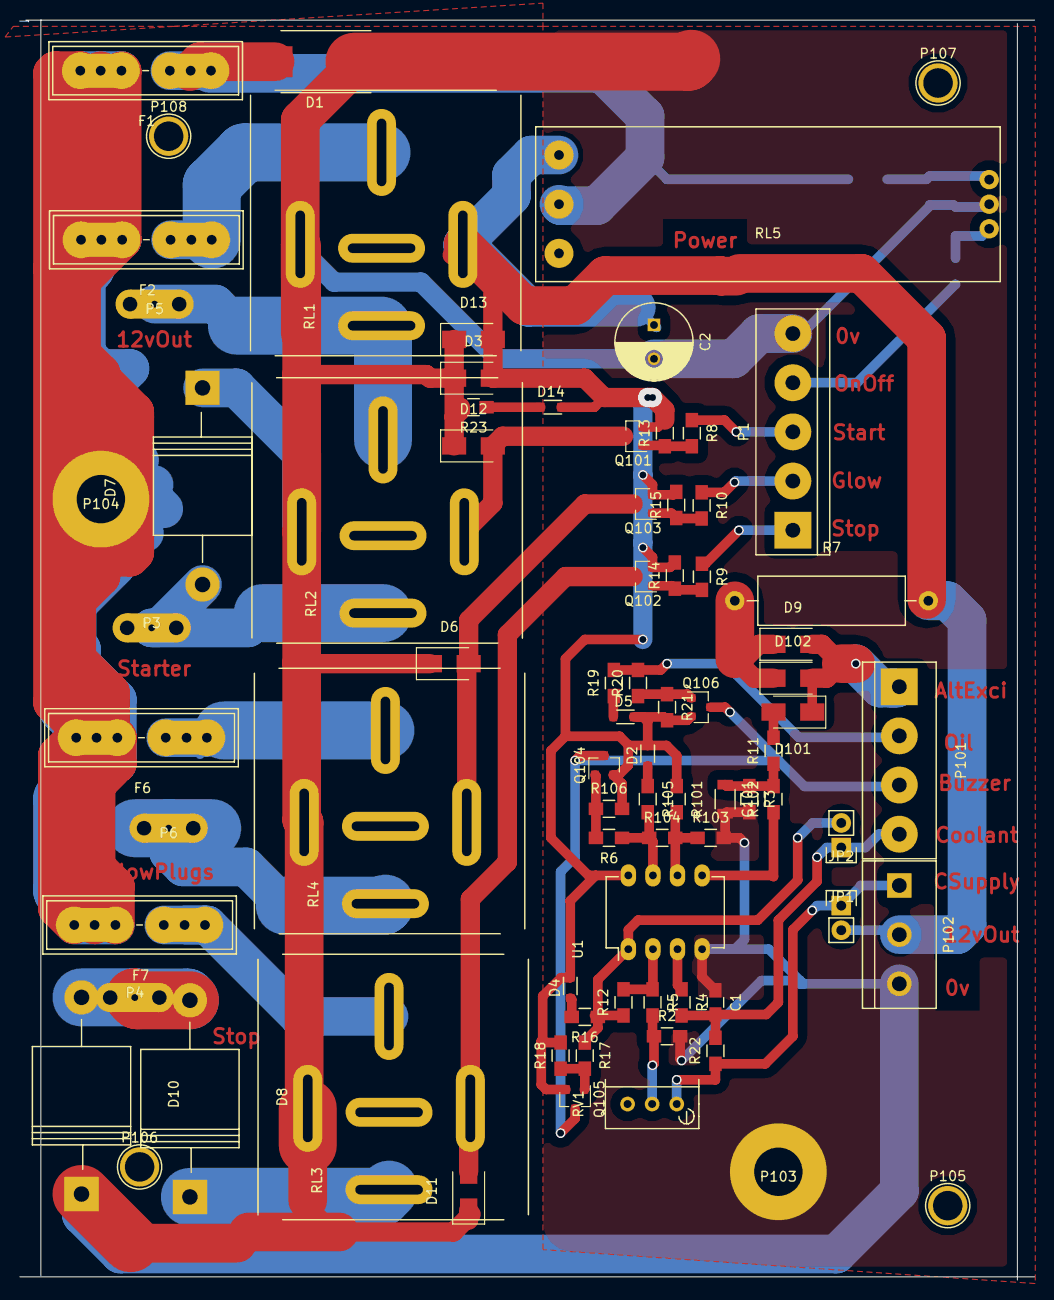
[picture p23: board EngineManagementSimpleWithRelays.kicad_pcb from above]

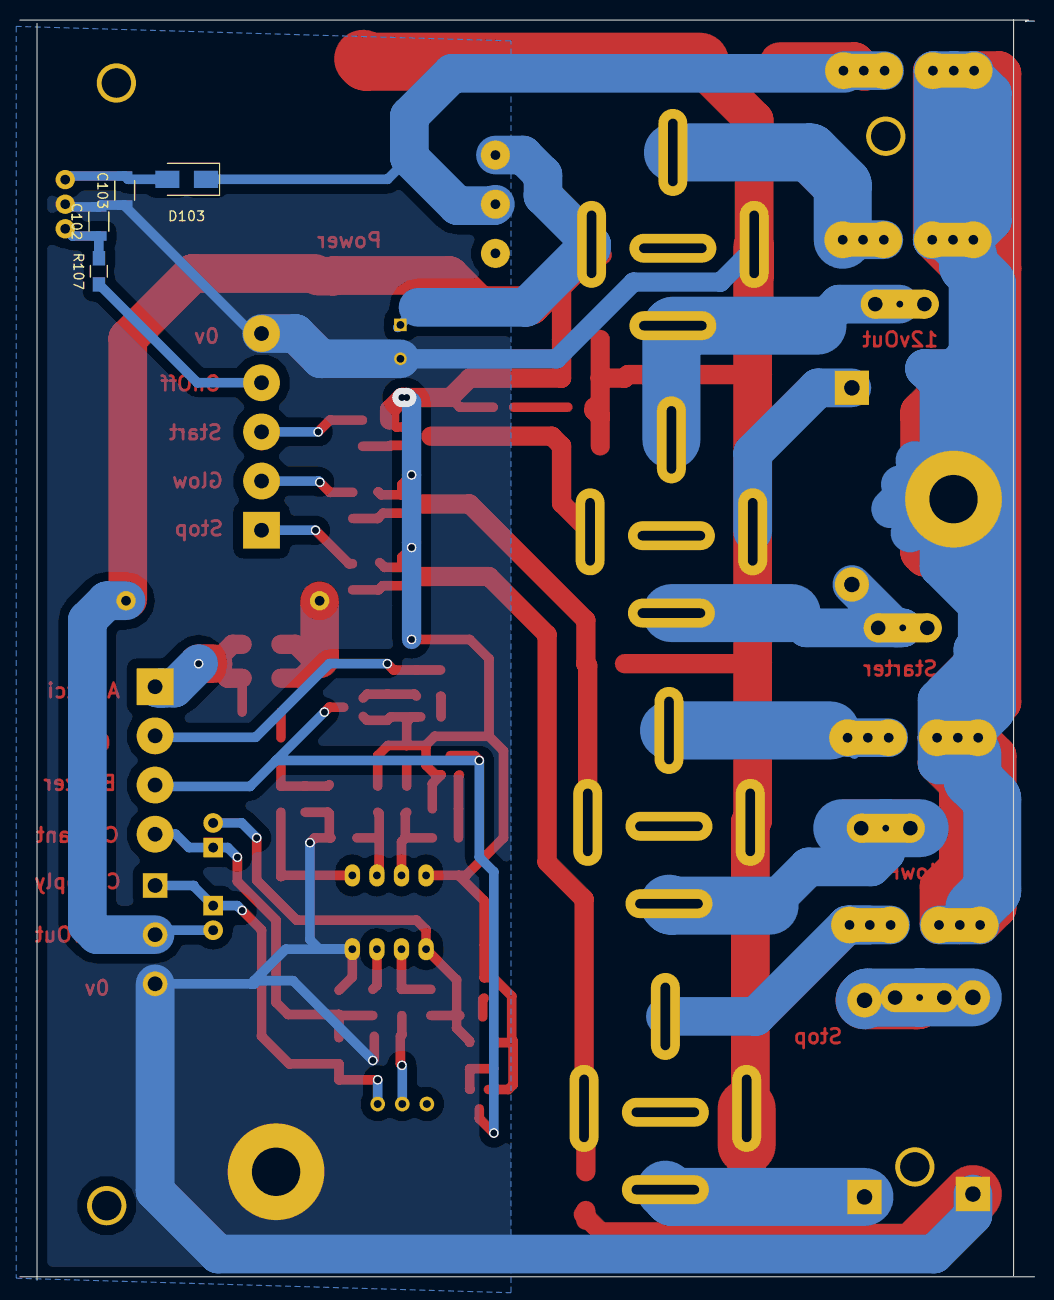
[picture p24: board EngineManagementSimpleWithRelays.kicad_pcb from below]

Board: 2 copper layers, 104.8 x 130.2 mm, 83 parts (4 on the bottom side), 46 nets.

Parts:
C1: 10nF; C_0805_HandSoldering
C2: 100uF; C_Radial_D8_L11.5_P3.5
C101, C103: 1uF; C_1206
C102: 100nF; C_1206
D1: SMBJ30CA-TR TSV; DO-214AB_Handsoldering
D2: ChargeWarn; D_0805
D3, D9, D102, D103: S1JL 1A 40V; D_SMA_Standard
D4: TempWarn; D_0805
D5, D14: OilWarn; D_0805
D6, D11, D12, D13: S1JL 1A 600V; D_SMA_Standard
D7: 5A 600V; Diode_P600_Horizontal
D8, D10: 10A 600V; Diode_P600_Horizontal
D101: SlJL 1A 40V; D_SMA_Standard
F1: FUSE 5A; BladeFuse-CarType
F2, F6: FUSE 30A; BladeFuse-CarType
F7: FUSE 15A; BladeFuse-CarType
JP1: UseSensorAlarm; Pin_Header_Straight_1x02
JP2: Use12vSupply; Pin_Header_Straight_1x02
P1: VPButtons; bornier5
P3: StarterSolenoidT30; CrimpBlade
P4: StopSolenoid; CrimpBlade
P5: 12VSwitchedPower; CrimpBlade
P6: GlowPlugs; CrimpBlade
P101: CONN_4; bornier4
P102: CONN_3; bornier3
P103: 0v; M5Bolt
P104: Battery+; M5Bolt
P105, P106, P107, P108: mount; 1pin
Q101, Q102, Q103, Q104, Q105, Q106: BC807-40; SOT-23
R2: 330R; R_0805_HandSoldering
R3: 1M; R_0805_HandSoldering
R4, R5, R6, R13, R14, R15, R17, R21, R101: 10K; R_0805_HandSoldering
R7: 10R; Resistor_Horizontal_RM20mm
R8, R9, R10, R18, R20, R106: 2.2K; R_0805_HandSoldering
R11, R16, R19, R22, R23, R102, R105, R107: 1K; R_0805_HandSoldering
R12: 10M; R_0805_HandSoldering
R103: 22K; R_0805_HandSoldering
R104: 100K; R_0805_HandSoldering
RL1: EnginePower; AutomotiveRelay35A
RL2: EngineStart; AutomotiveRelay35A
RL3: EngineStop; AutomotiveRelay35A
RL4: GlowPlugs; AutomotiveRelay35A
RL5: LatchingRelay
RV1: 10K; Potentiometer_Bourns_3296W_3-8Zoll_Inline_ScrewUp
U1: LM358; DIP-8_W7.62mm_LongPads

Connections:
12vSwitched: C2.1, D2.1, D3.2, D4.1, D5.1, D13.2, D14.1, JP2.2, P102.2, Q101.2, Q102.2, Q103.2, Q104.2, Q105.2, Q106.2, R7.2, R13.2, R14.2, R15.2, R18.2, R21.2, R101.1, R106.2, RL1.86, RL5.6, U1.8
AlternatorExcitation: D9.2, D101.1, D102.2, P101.1
Battery+: F1.2, F2.2, F6.2, F7.2, P104.1
BatteryFused5A: D1.2, D103.1, F1.1, RL5.4
Buzzer: P101.3, Q104.3, Q105.3, Q106.3
CoolantSensorSupply: JP2.1, P102.1, R22.1, RV1.1
CoolantTemp: C1.2, JP1.1, P101.4, R4.2, R22.2
GND: C1.1, C2.2, C101.2, C102.2, C103.1, D1.1, D3.1, D6.1, D7.1, D10.1, D11.1, D12.1, D13.1, P1.5, P102.3, P103.1, R2.2, R3.2, R23.2, R103.2, RL1.85, RL2.85, RL3.85, RL4.85, RL5.3, U1.4
GlowBtn: P1.2, R10.1
GlowCoil: D6.2, Q103.3, RL4.86
GlowPlugs: P6.1, RL4.87
unnamed: C101.1, R3.1, R11.1, R102.2
unnamed: C102.1, R107.2, RL5.2
unnamed: C103.2, D103.2, RL5.1
unnamed: D2.2, R105.1
unnamed: D4.2, R16.2
unnamed: D5.2, R19.1
unnamed: D8.1, RL3.87
unnamed: D14.2, R23.1
unnamed: D101.2, R11.2
unnamed: D9.1, D102.1, R7.1
unnamed: F2.1, RL1.30
unnamed: P5.1, RL1.87, RL2.30
unnamed: F6.1, RL4.30
unnamed: F7.1, RL3.30
unnamed: JP1.2, R12.1, R16.1, R17.1, U1.1
unnamed: Q101.1, R8.2, R13.1
unnamed: Q102.1, R9.2, R14.1
unnamed: Q103.1, R10.2, R15.1
unnamed: Q104.1, R6.2, R106.1
unnamed: Q105.1, R17.2, R18.1
unnamed: Q106.1, R20.1, R21.1
unnamed: R2.1, R5.2, RV1.2
unnamed: R4.1, U1.3
unnamed: R5.1, R12.2, U1.2
unnamed: R101.2, R103.1, R104.2, U1.6
unnamed: R102.1, U1.5
unnamed: R6.1, R104.1, R105.2, U1.7
OilSwitch: P101.2, R19.2, R20.2
OnOffBtn: P1.4, R107.1
StartBtn: P1.3, R8.1
StartCoil: D12.2, Q101.3, RL2.86
StarterSolenoidT30: D7.2, P3.1, RL2.87
StopBtn: P1.1, R9.1
StopCoil: D11.2, Q102.3, RL3.86
StopSolenoid: D8.2, D10.2, P4.1

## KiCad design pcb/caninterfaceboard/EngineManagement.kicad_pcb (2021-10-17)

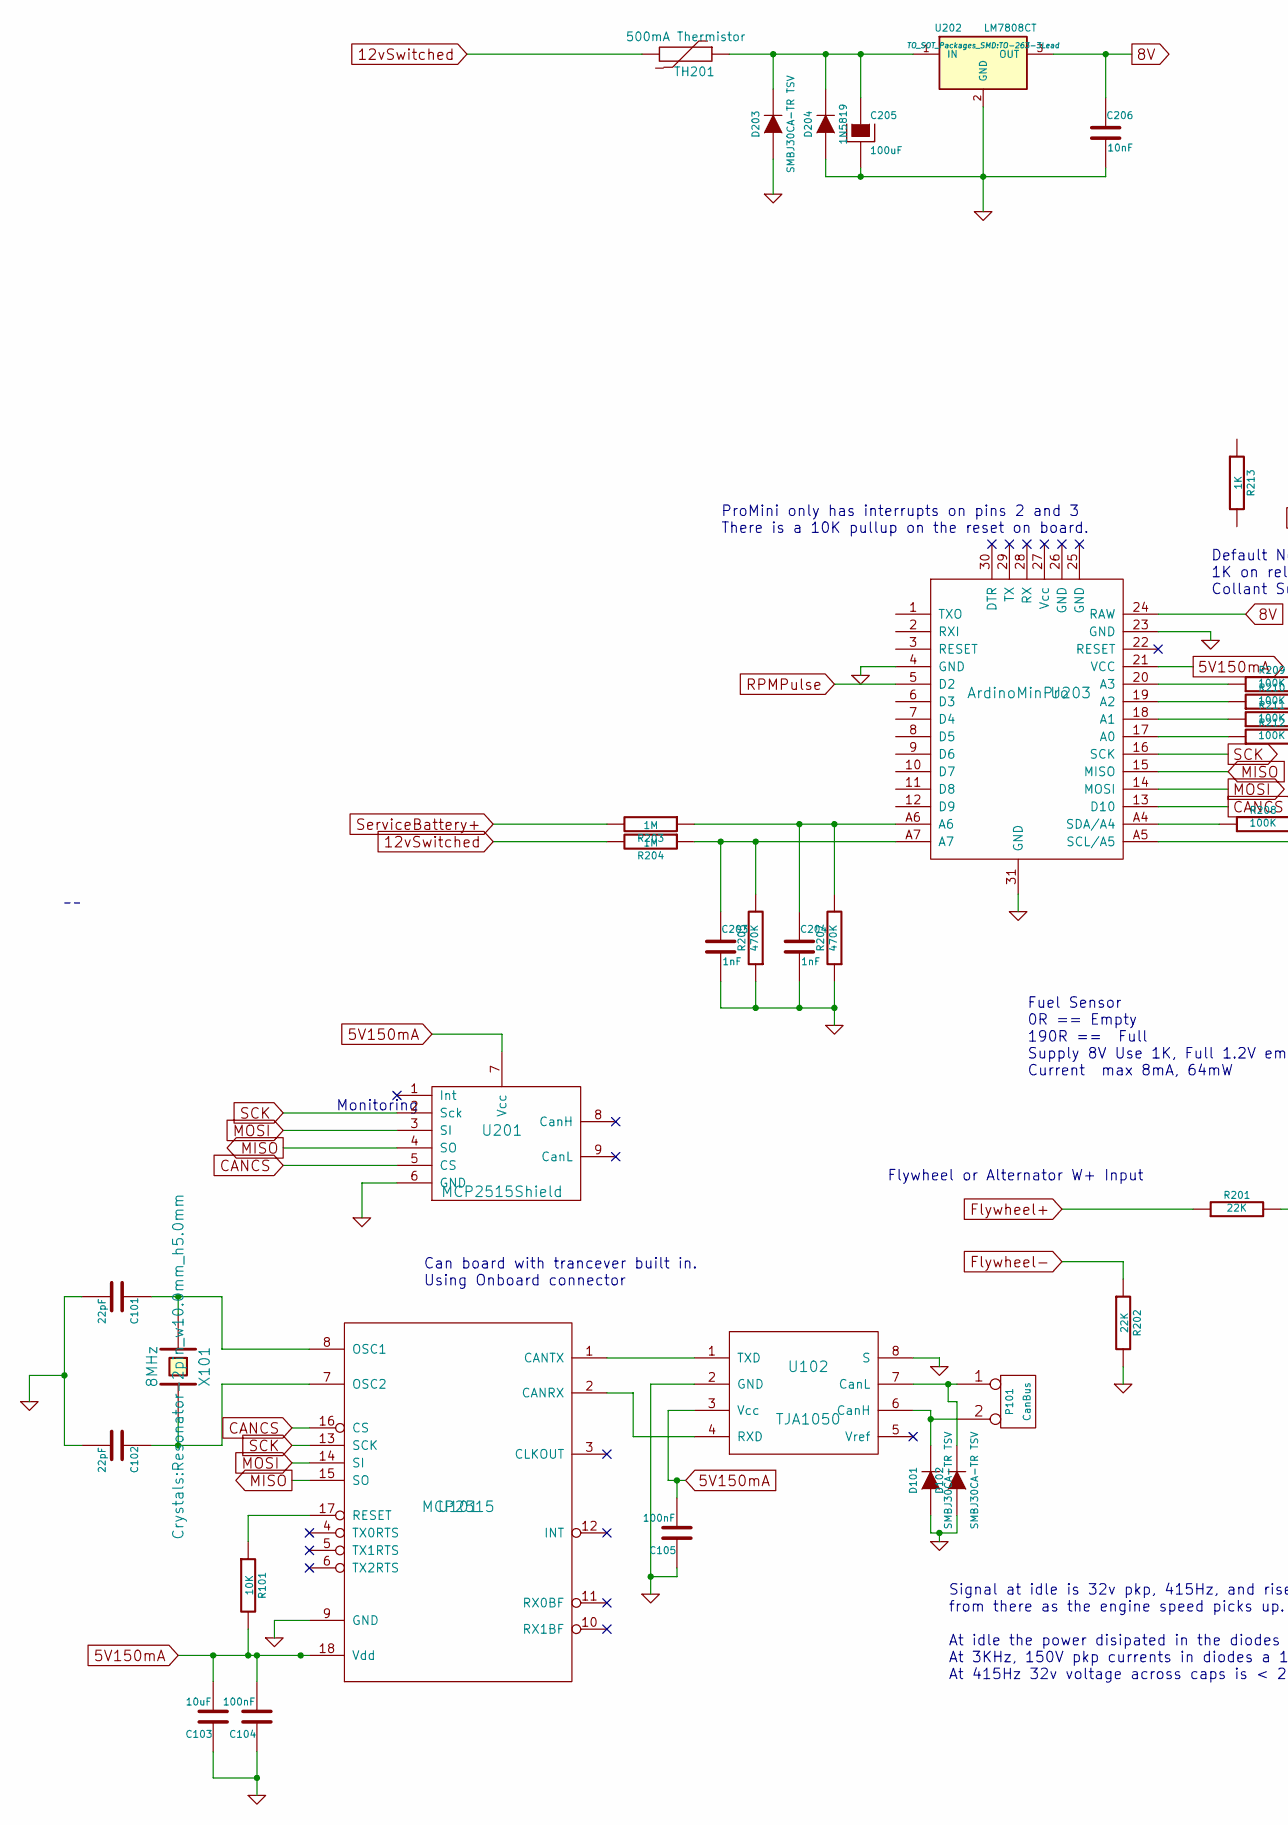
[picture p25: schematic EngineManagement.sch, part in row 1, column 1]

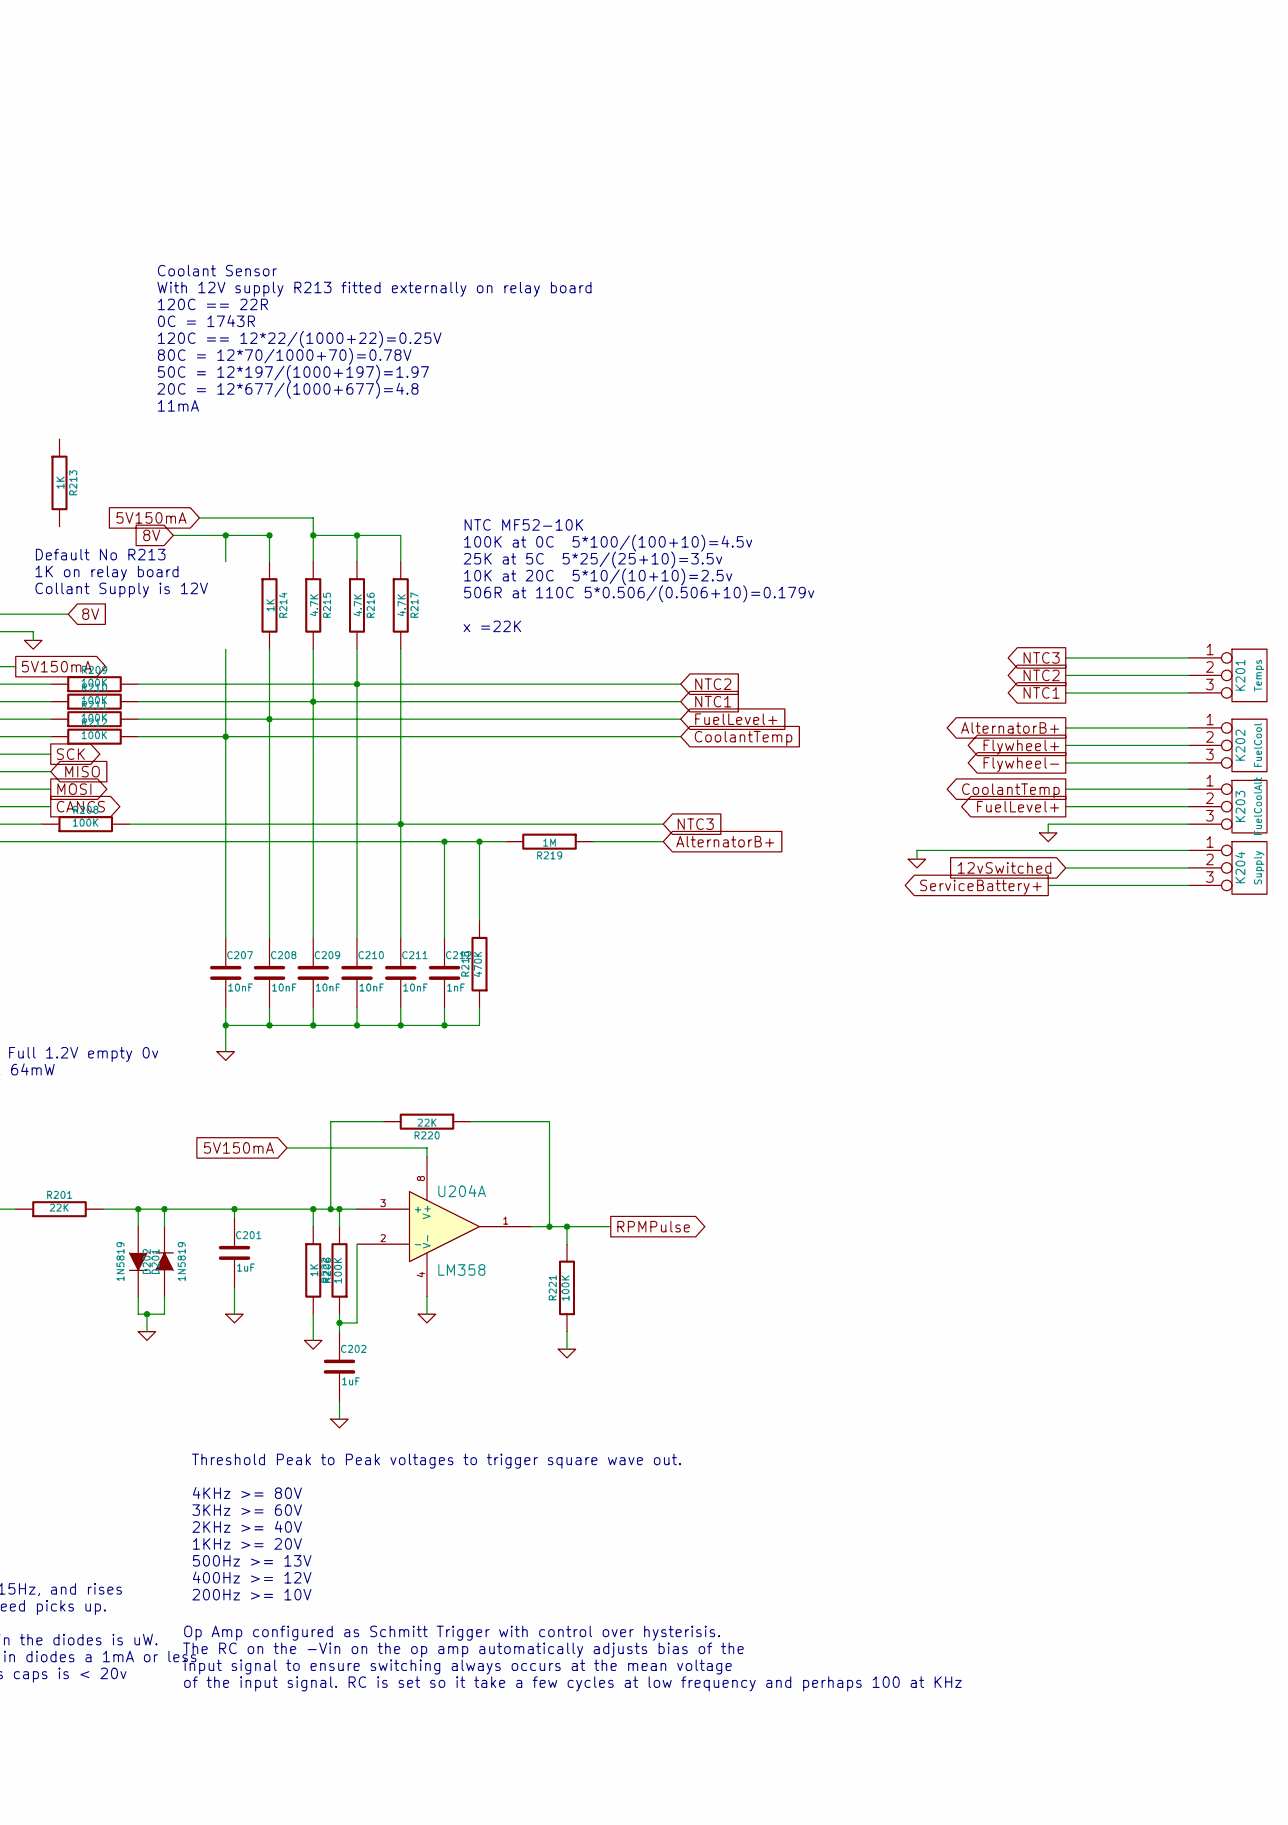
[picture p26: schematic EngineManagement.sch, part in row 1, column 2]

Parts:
C101, C102: 22pF; R_0603_HandSoldering
C103: 10uF; R_1206_HandSoldering
C104, C105: 100nF; C_0805_HandSoldering
C201, C202: 1uF; C_1210
C203, C204, C212: 1nF; C_0805_HandSoldering
C205: 100uF; C_Radial_D8_L11.5_P3.5
C206, C207, C208, C209, C210, C211: 10nF; C_0805_HandSoldering
D101, D102, D203: SMBJ30CA-TR TSV; DO-214AB_Handsoldering
D201, D202: 1N5819; D_SOD-123
D204: 1N5819; Resistor_Horizontal_RM7mm
K201: Temps; bornier3
K202: FuelCool; bornier3
K203: FuelCoolAlt; bornier3
K204: Supply; bornier3
P101: CanBus; bornier2
R101: 10K; R_0805_HandSoldering
R201, R202, R220: 22K; R_0805_HandSoldering
R203, R204, R219: 1M; R_0805_HandSoldering
R205, R207, R218: 470K; R_0805_HandSoldering
R206, R213, R214: 1K; R_0805_HandSoldering
R208, R209, R210, R211, R212, R221, R222: 100K; R_0805_HandSoldering
R215, R216, R217: 4.7K; R_0805_HandSoldering
TH201: 500mA Thermistor; Resistor_Horizontal_RM7mm
U101: MCP2515; SOIC-18W_7.5x11.6mm_Pitch1.27mm
U102: TJA1050; SOIC-8_3.9x4.9mm_Pitch1.27mm
U201: MCP2515Shield; MCP2515Board
U202: LM7808CT; TO-263-3Lead
U203: ArdinoMinPro; ArduinoProMini
U204: LM358; DIP-8_W7.62mm_LongPads
X101: 8MHz; Resonator-2pin_w10.0mm_h5.0mm

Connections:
5V150mA: C103.2, C104.2, C105.2, R101.2, R215.1, R216.1, R217.1, U101.18 (Vdd), U102.3 (Vcc), U201.7 (Vcc), U203.21 (VCC), U204.8 (V+)
8V: C206.1, R213.1, R214.1, U202.3 (OUT), U203.24 (RAW)
12vSwitched: K204.2 (PM), R204.2, TH201.2
AlternatorB+: K202.1, R219.1
CANCS: U101.16 (CS), U201.5 (CS), U203.13 (D10)
CoolantTemp: C207.1, K203.1, R212.2, R213.2
Flywheel+: K202.2 (PM), R201.1
Flywheel-: K202.3, R202.1
FuelLevel+: C208.1, K203.2 (PM), R211.2, R214.2
GND: C101.2, C102.2, C103.1, C104.1, C105.1, C201.2, C202.2, C203.2, C204.2, C205.2, C206.2, C207.2, C208.2, C209.2, C210.2, C211.2, C212.2, D101.1 (A), D102.1 (A), D201.2 (K), D202.1 (A), D203.1 (A), D204.1 (A), K203.3, K204.1, R202.2, R205.1, R206.2, R207.1, R218.1, R221.1, U101.9 (GND), U102.2 (GND), U102.8 (S), U201.6 (GND), U202.2 (GND), U203.4 (GND), U203.23 (GND), U203.31 (GND), U204.4 (V-)
MISO: U101.15 (SO), U201.4 (SO), U203.15 (MISO)
MOSI: U101.14 (SI), U201.3 (SI), U203.14 (MOSI)
NTC1: C209.1, K201.3, R210.2, R215.2
NTC2: C210.1, K201.2 (PM), R209.2, R216.2
NTC3: C211.1, K201.1, R208.2, R217.2
unnamed: C101.1, U101.8 (OSC1), X101.1
unnamed: C102.1, U101.7 (OSC2), X101.2
unnamed: C201.1, D201.1 (A), D202.2 (K), R201.2, R206.1, R220.2, R222.2, U204.3 (+)
unnamed: C202.1, R222.1, U204.2 (-)
unnamed: C203.1, R204.1, R205.2, U203.A7
unnamed: C204.1, R203.1, R207.2, U203.A6
unnamed: C205.1, D203.2 (K), D204.2 (K), TH201.1, U202.1 (IN)
unnamed: C212.1, R218.2, R219.2, U203.A5 (SCL/A5)
unnamed: D101.2 (K), P101.2 (PM), U102.6 (CanH)
unnamed: D102.2 (K), P101.1, U102.7 (CanL)
unnamed: R101.1, U101.17 (RESET)
unnamed: R208.1, U203.A4 (SDA/A4)
unnamed: R209.1, U203.20 (A3)
unnamed: R210.1, U203.19 (A2)
unnamed: R211.1, U203.18 (A1)
unnamed: R212.1, U203.17 (A0)
unnamed: U101.1 (CANTX), U102.1 (TXD)
unnamed: U101.2 (CANRX), U102.4 (RXD)
RPMPulse: R220.1, R221.2, U203.5 (D2), U204.1
SCK: U101.13 (SCK), U201.2 (Sck), U203.16 (SCK)
ServiceBattery+: K204.3, R203.2

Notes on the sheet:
Monitoring
Fuel Sensor 0R == Empty 190R == Full Supply 8V Use 1K, Full 1.2V empty 0v Current max 8mA, 64mW
Can board with trancever built in. Using Onboard connector
ProMini only has interrupts on pins 2 and 3 There is a 10K pullup on the reset on board.
Signal at idle is 32v pkp, 415Hz, and rises from there as the engine speed picks up. At idle the power disipated in the diodes is uW. At 3KHz, 150V pkp currents in diodes a 1mA or less At 415Hz 32v voltage across caps is < 20v
NTC MF52-10K 100K at 0C 5*100/(100+10)=4.5v 25K at 5C 5*25/(25+10)=3.5v 10K at 20C 5*10/(10+10)=2.5v 506R at 110C 5*0.506/(0.506+10)=0.179v x =22K
Coolant Sensor With 12V supply R213 fitted externally on relay board 120C == 22R 0C = 1743R 120C == 12*22/(1000+22)=0.25V 80C = 12*70/1000+70)=0.78V 50C = 12*197/(1000+197)=1.97 20C = 12*677/(1000+677)=4.8 11mA
Flywheel or Alternator W+ Input
Op Amp configured as Schmitt Trigger with control over hysterisis. The RC on the -Vin on the op amp automatically adjusts bias of the input signal to ensure switching always occurs at the mean voltage of the input signal. RC is set so it take a few cycles at low frequency and perhaps 100 at KHz
Threshold Peak to Peak voltages to trigger square wave out. 4KHz >= 80V 3KHz >= 60V 2KHz >= 40V 1KHz >= 20V 500Hz >= 13V 400Hz >= 12V 200Hz >= 10V
Default No R213 1K on relay board Collant Supply is 12V

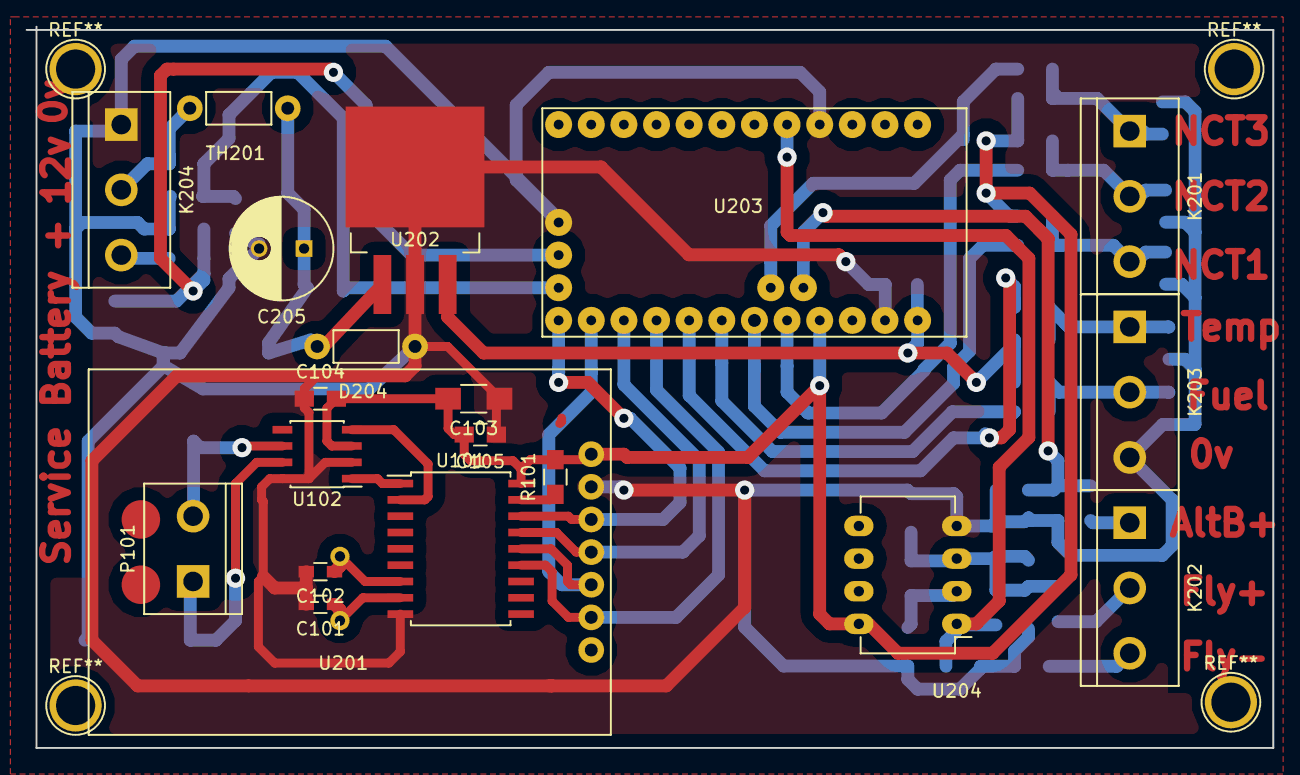
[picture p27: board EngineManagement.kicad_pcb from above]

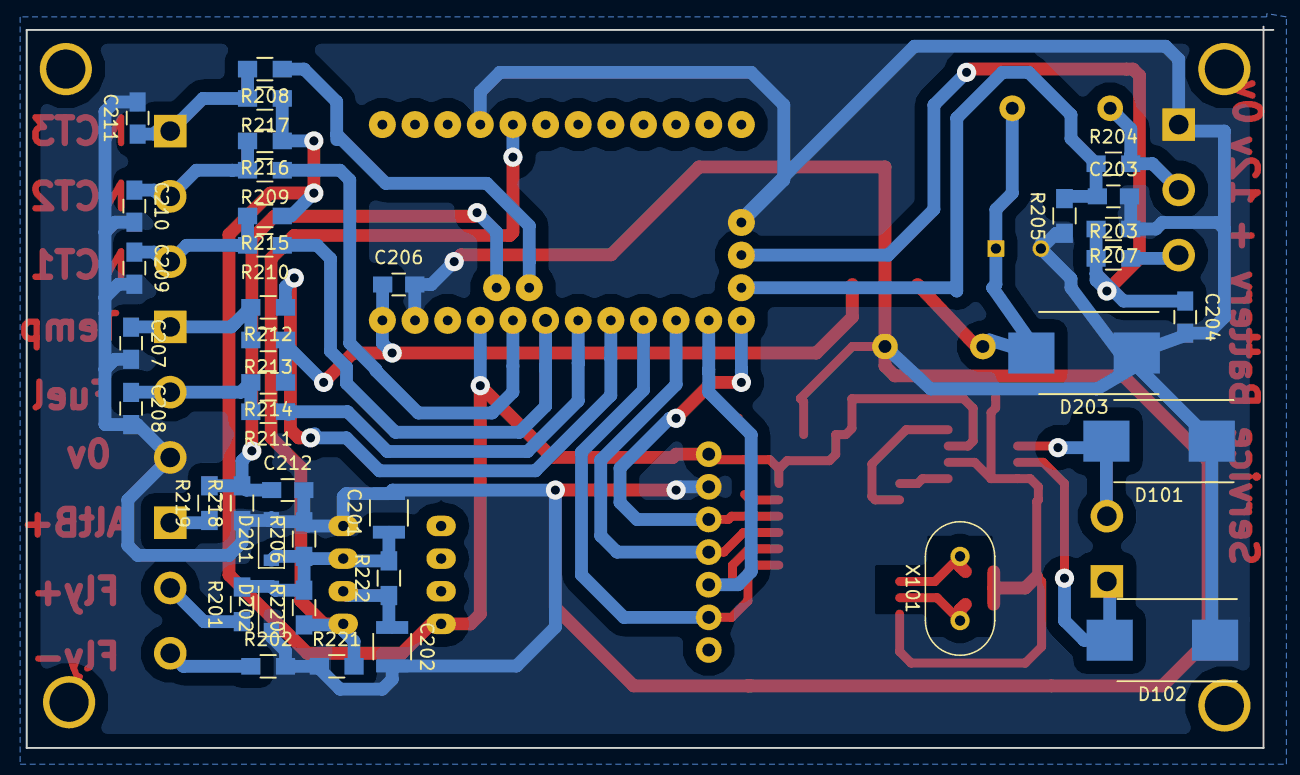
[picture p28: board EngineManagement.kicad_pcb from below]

Board: 2 copper layers, 97.0 x 56.1 mm, 59 parts (39 on the bottom side), 36 nets.

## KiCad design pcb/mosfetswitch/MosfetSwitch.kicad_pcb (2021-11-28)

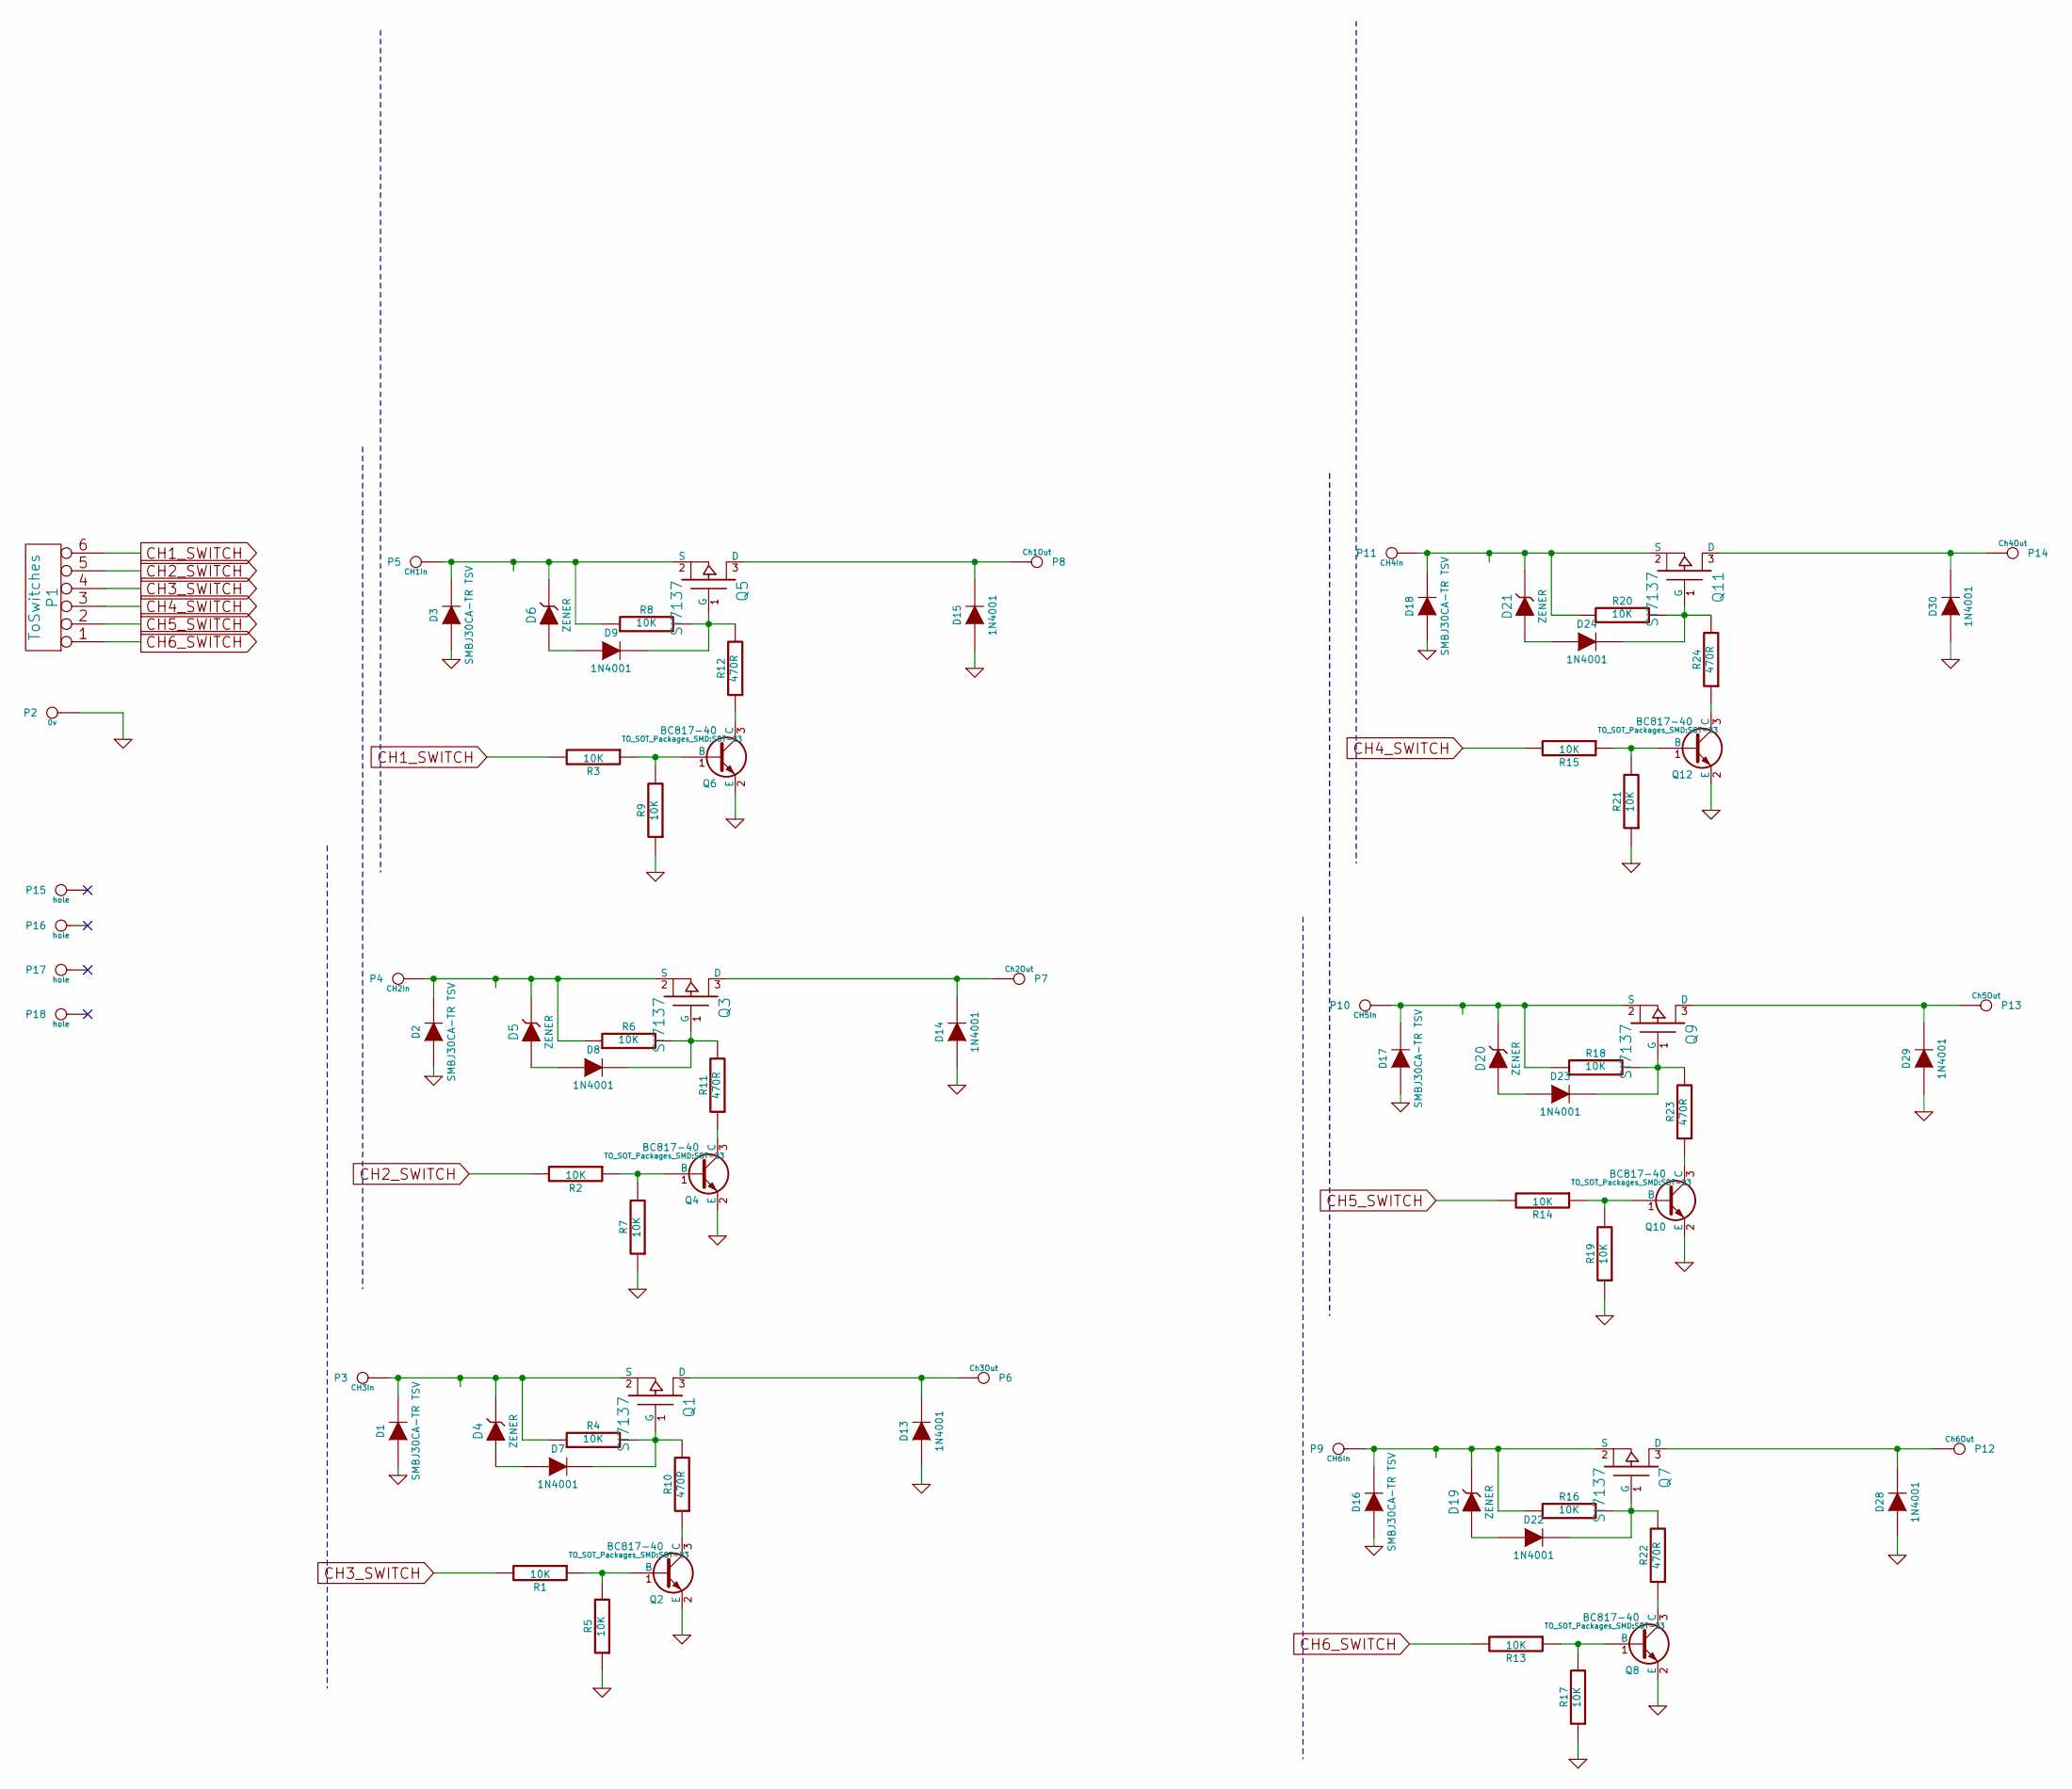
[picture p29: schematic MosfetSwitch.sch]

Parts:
D1, D2, D3, D16, D17, D18: SMBJ30CA-TR TSV; DO-214AB_Handsoldering
D4, D5, D6, D19, D20, D21: ZENER; D_SOD-123
D7, D8, D9, D22, D23, D24: 1N4001; D_SOD-123
D13, D14, D15, D28, D29, D30: 1N4001; Resistor_Horizontal_RM7mm
P1: ToSwitches; bornier6
P2: 0v; CrimpBlade
P3: CH3In; CrimpBlade
P4: CH2In; CrimpBlade
P5: CH1In; CrimpBlade
P6: Ch3Out; CrimpBlade
P7: Ch2Out; CrimpBlade
P8: Ch1Out; CrimpBlade
P9: CH6In; CrimpBlade
P10: CH5In; CrimpBlade
P11: CH4In; CrimpBlade
P12: Ch6Out; CrimpBlade
P13: Ch5Out; CrimpBlade
P14: Ch4Out; CrimpBlade
P15, P16, P17, P18: hole; 1pin
Q1, Q3, Q5, Q7, Q9, Q11: SI7137; Si7137PowerPak
Q2, Q4, Q6, Q8, Q10, Q12: BC817-40; SOT-23
R1, R2, R3, R4, R5, R6, R7, R8, R9, R13, R14, R15, R16, R17, R18, R19, R20, R21: 10K; R_0805_HandSoldering
R10, R11, R12, R22, R23, R24: 470R; R_0805_HandSoldering

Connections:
CH1_SWITCH: P1.6, R3.2
CH2_SWITCH: P1.5, R2.2
CH3_SWITCH: P1.4, R1.2
CH4_SWITCH: P1.3, R15.2
CH5_SWITCH: P1.2, R14.2
CH6_SWITCH: P1.1, R13.2
GND: D1.1 (A), D2.1 (A), D3.1 (A), D13.1 (A), D14.1 (A), D15.1 (A), D16.1 (A), D17.1 (A), D18.1 (A), D28.1 (A), D29.1 (A), D30.1 (A), P2.1, Q2.2 (E), Q4.2 (E), Q6.2 (E), Q8.2 (E), Q10.2 (E), Q12.2 (E), R5.1, R7.1, R9.1, R17.1, R19.1, R21.1
unnamed: D1.2 (K), D4.2 (K), P3.1, Q1.2 (S), R4.1
unnamed: D2.2 (K), D5.2 (K), P4.1, Q3.2 (S), R6.1
unnamed: D3.2 (K), D6.2 (K), P5.1, Q5.2 (S), R8.1
unnamed: D4.1 (A), D7.1 (A)
unnamed: D5.1 (A), D8.1 (A)
unnamed: D6.1 (A), D9.1 (A)
unnamed: D7.2 (K), Q1.1 (G), R4.2, R10.2
unnamed: D8.2 (K), Q3.1 (G), R6.2, R11.2
unnamed: D9.2 (K), Q5.1 (G), R8.2, R12.2
unnamed: D13.2 (K), P6.1, Q1.3 (D)
unnamed: D14.2 (K), P7.1, Q3.3 (D)
unnamed: D15.2 (K), P8.1, Q5.3 (D)
unnamed: D16.2 (K), D19.2 (K), P9.1, Q7.2 (S), R16.1
unnamed: D17.2 (K), D20.2 (K), P10.1, Q9.2 (S), R18.1
unnamed: D18.2 (K), D21.2 (K), P11.1, Q11.2 (S), R20.1
unnamed: D19.1 (A), D22.1 (A)
unnamed: D20.1 (A), D23.1 (A)
unnamed: D21.1 (A), D24.1 (A)
unnamed: D22.2 (K), Q7.1 (G), R16.2, R22.2
unnamed: D23.2 (K), Q9.1 (G), R18.2, R23.2
unnamed: D24.2 (K), Q11.1 (G), R20.2, R24.2
unnamed: D28.2 (K), P12.1, Q7.3 (D)
unnamed: D29.2 (K), P13.1, Q9.3 (D)
unnamed: D30.2 (K), P14.1, Q11.3 (D)
unnamed: Q2.1 (B), R1.1, R5.2
unnamed: Q2.3 (C), R10.1
unnamed: Q4.1 (B), R2.1, R7.2
unnamed: Q4.3 (C), R11.1
unnamed: Q6.1 (B), R3.1, R9.2
unnamed: Q6.3 (C), R12.1
unnamed: Q8.1 (B), R13.1, R17.2
unnamed: Q8.3 (C), R22.1
unnamed: Q10.1 (B), R14.1, R19.2
unnamed: Q10.3 (C), R23.1
unnamed: Q12.1 (B), R15.1, R21.2
unnamed: Q12.3 (C), R24.1

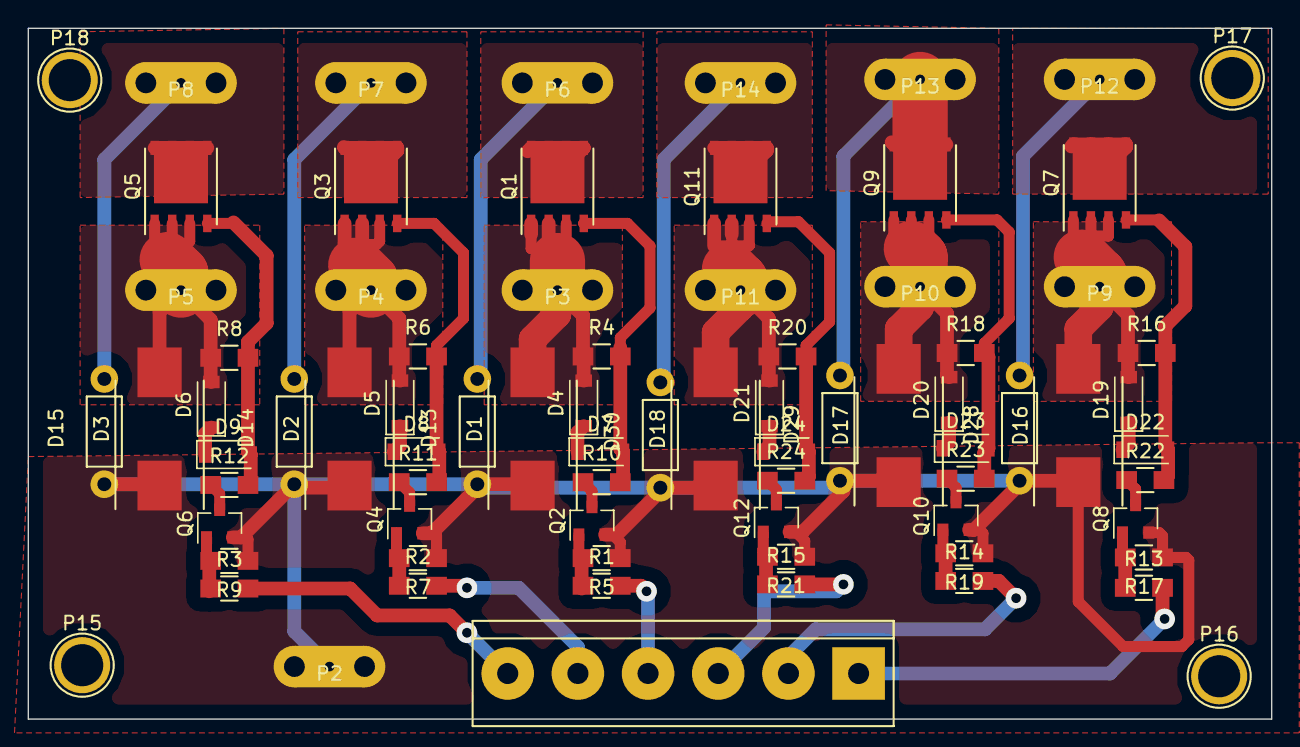
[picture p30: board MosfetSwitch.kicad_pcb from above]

Board: 2 copper layers, 90.0 x 50.0 mm, 78 parts (0 on the bottom side), 43 nets.

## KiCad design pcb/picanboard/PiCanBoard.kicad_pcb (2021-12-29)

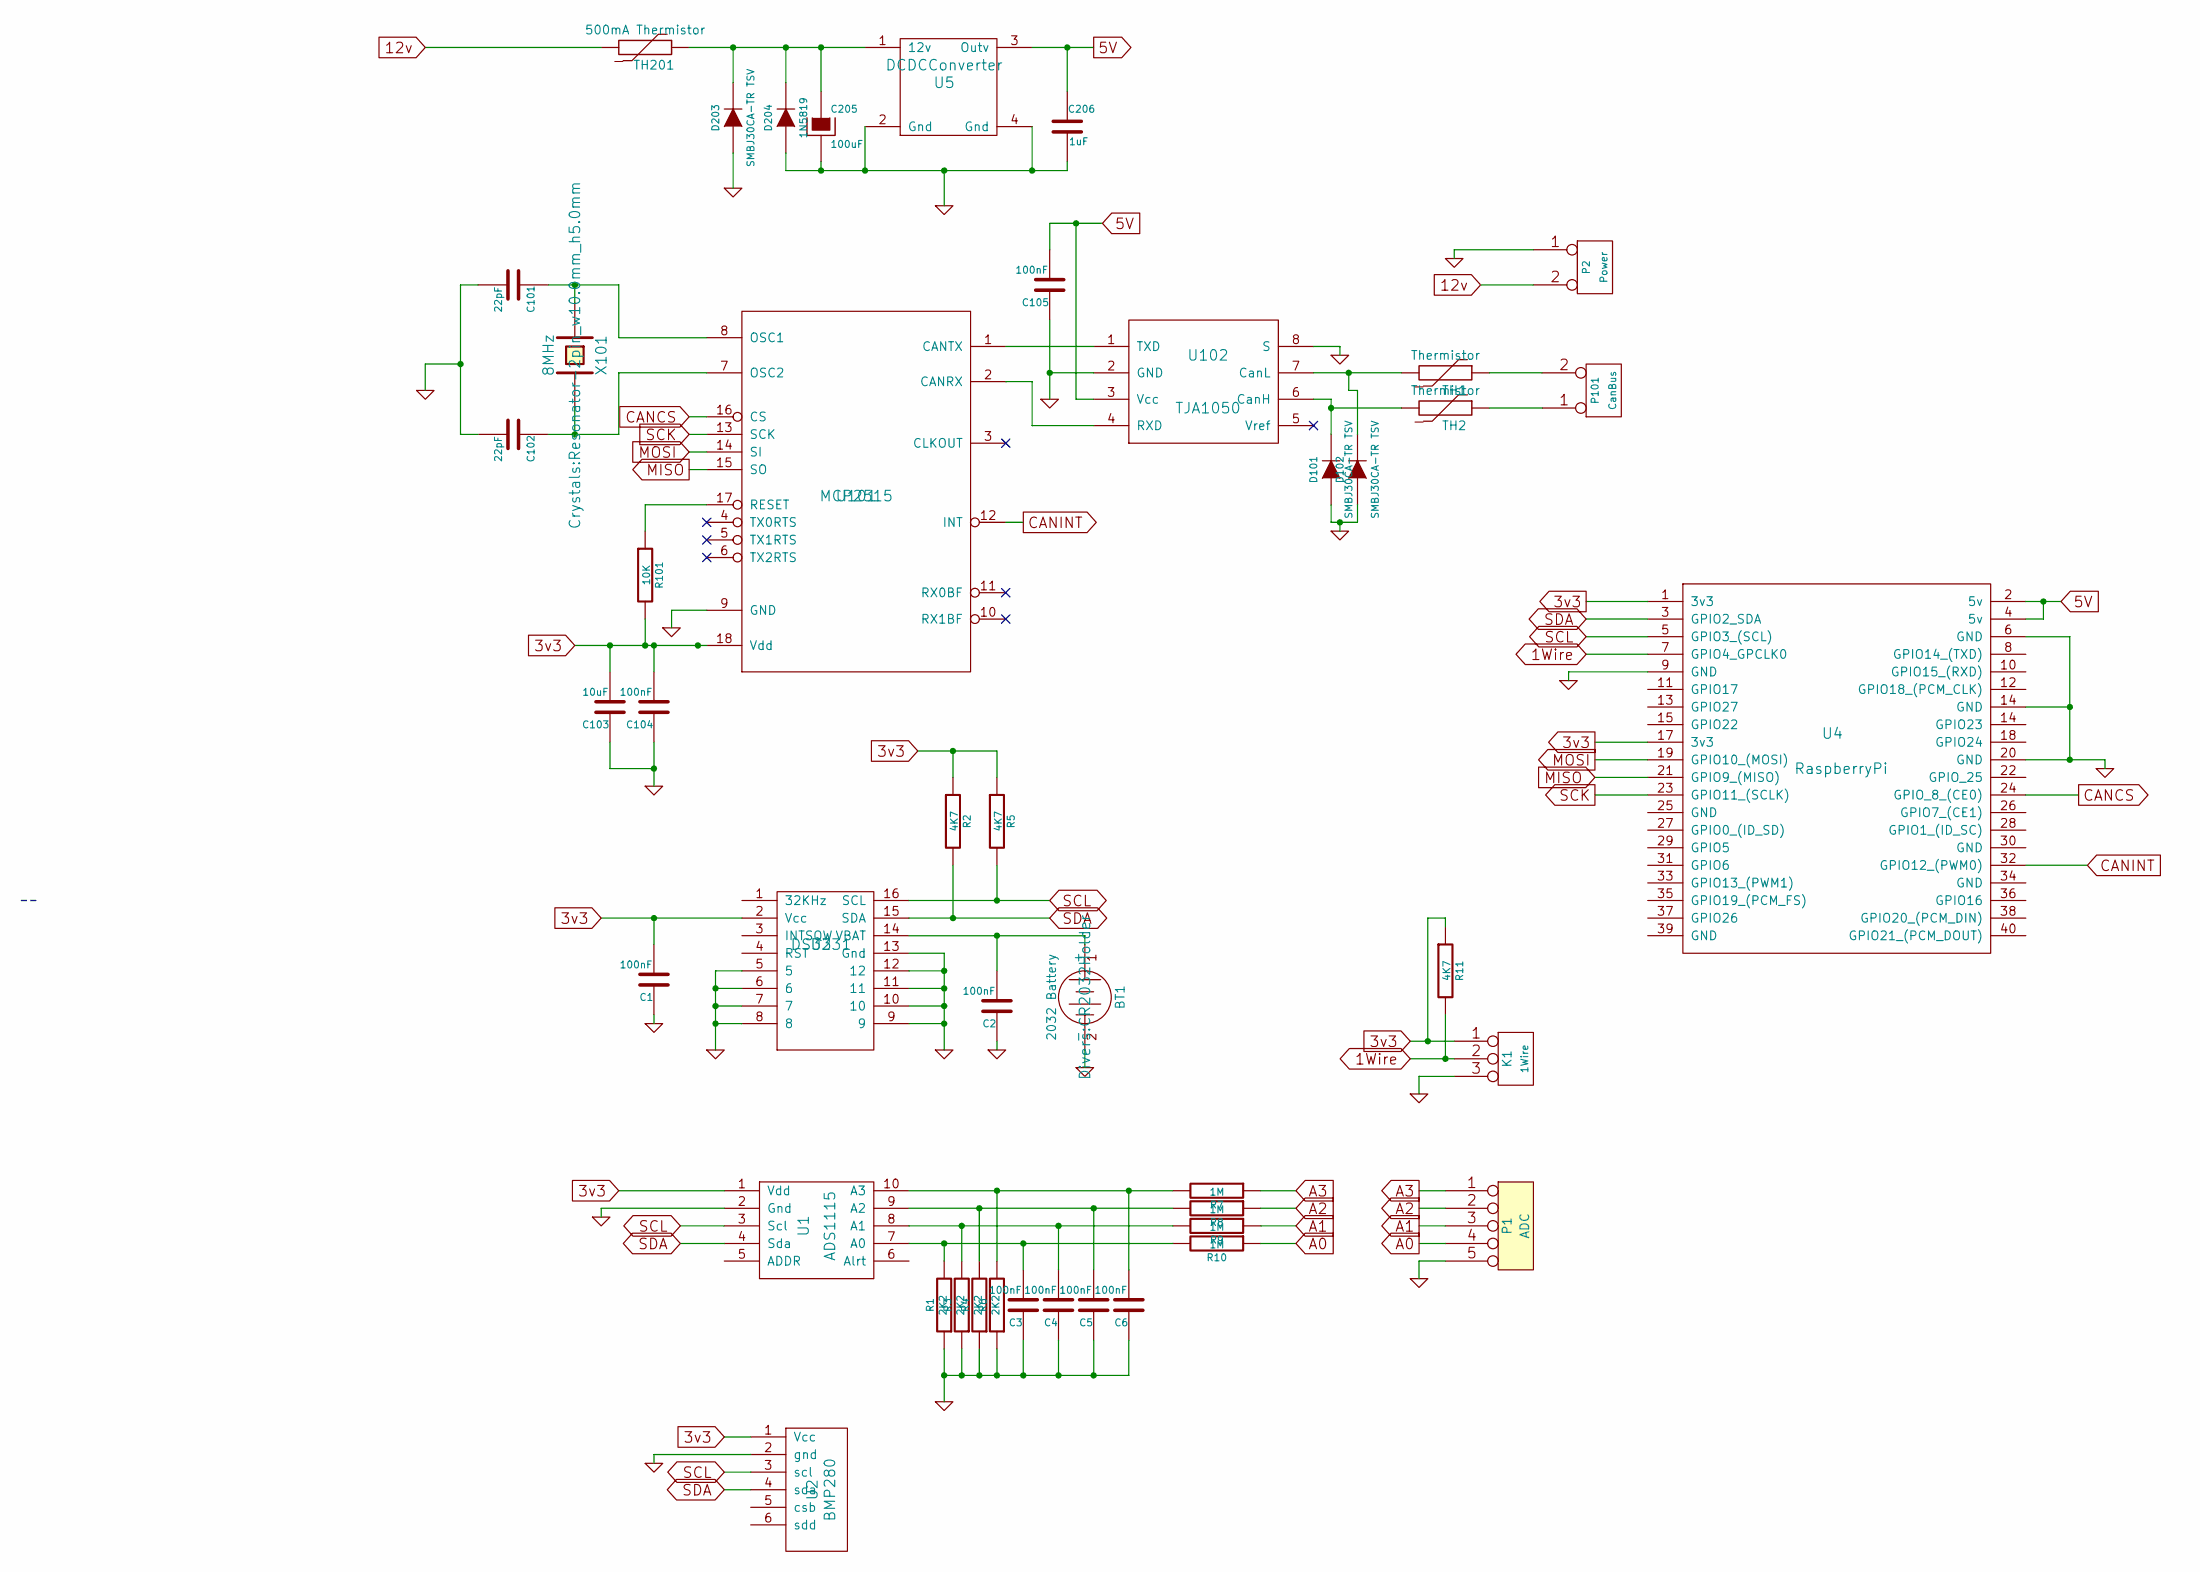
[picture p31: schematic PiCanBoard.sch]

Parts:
BT1: 2032 Battery; CR2032Holder
C1, C2, C3, C4, C5, C6, C104, C105: 100nF; C_0805_HandSoldering
C101, C102: 22pF; R_0603_HandSoldering
C103: 10uF; R_1206_HandSoldering
C205: 100uF; C_1210_HandSoldering
C206: 1uF; C_1210_HandSoldering
D101, D102, D203: SMBJ30CA-TR TSV; DO-214AB_Handsoldering
D204: 1N5819; DO-214AB_Handsoldering
K1: 1Wire; bornier3
P1: ADC; bornier5
P2: Power; bornier2
P101: CanBus; bornier2
R1, R3, R4, R6: 2K2; R_0805_HandSoldering
R2, R5, R11: 4K7; R_0805_HandSoldering
R7, R8, R9, R10: 1M; R_0805_HandSoldering
R101: 10K; R_0805_HandSoldering
TH1, TH2: Thermistor; R_1210
TH201: 500mA Thermistor; Resistor_Horizontal_RM7mm
U1: ADS1115
U2: BMP280
U3: DS3231; SOIC-16W_7.5x10.3mm_Pitch1.27mm
U4: RaspberryPi; PiZeroW
U5: DCDCConverter; DC-DC-Converter
U101: MCP2515; SOIC-18W_7.5x11.6mm_Pitch1.27mm
U102: TJA1050; SOIC-8_3.9x4.9mm_Pitch1.27mm
X101: 8MHz; Resonator-2pin_w10.0mm_h5.0mm

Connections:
1Wire: K1.2 (PM), R11.2, U4.7 (GPIO4_GPCLK0)
3v3: C1.2, C103.2, C104.2, K1.1, R2.1, R5.1, R11.1, R101.2, U1.1 (Vdd), U2.1 (Vcc), U3.2 (Vcc), U4.1 (3v3), U4.17 (3v3), U101.18 (Vdd)
5V: C105.2, C206.1, U4.2 (5v), U4.4 (5v), U5.3 (Outv), U102.3 (Vcc)
12v: P2.2 (PM), TH201.2
A0: P1.4, R10.1
A1: P1.3, R9.1
A2: P1.2, R8.1
A3: P1.1, R7.1
CANCS: U4.24 (GPIO_8_(CE0)), U101.16 (CS)
CANINT: U4.32 (GPIO12_(PWM0)), U101.12 (INT)
GND: BT1.2 (-), C1.1, C2.1, C3.1, C4.1, C5.1, C6.1, C101.2, C102.2, C103.1, C104.1, C105.1, C205.2, C206.2, D101.1 (A), D102.1 (A), D203.1 (A), D204.1 (A), K1.3, P1.5, P2.1, R1.1, R3.1, R4.1, R6.1, U1.2 (Gnd), U2.2 (gnd), U3.5, U3.6, U3.7, U3.8, U3.9, U3.10, U3.11, U3.12, U3.13 (Gnd), U4.6 (GND), U4.9 (GND), U4.14 (GND), U4.20 (GND), U5.2 (Gnd), U5.4 (Gnd), U101.9 (GND), U102.2 (GND), U102.8 (S)
MISO: U4.21 (GPIO9_(MISO)), U101.15 (SO)
MOSI: U4.19 (GPIO10_(MOSI)), U101.14 (SI)
unnamed: BT1.1 (+), C2.2, U3.14 (VBAT)
unnamed: C3.2, R1.2, R10.2, U1.7 (A0)
unnamed: C4.2, R3.2, R9.2, U1.8 (A1)
unnamed: C5.2, R4.2, R8.2, U1.9 (A2)
unnamed: C6.2, R6.2, R7.2, U1.10 (A3)
unnamed: C101.1, U101.8 (OSC1), X101.1
unnamed: C102.1, U101.7 (OSC2), X101.2
unnamed: C205.1, D203.2 (K), D204.2 (K), TH201.1, U5.1 (12v)
unnamed: D101.2 (K), TH2.2, U102.6 (CanH)
unnamed: D102.2 (K), TH1.2, U102.7 (CanL)
unnamed: P101.1, TH2.1
unnamed: P101.2 (PM), TH1.1
unnamed: R101.1, U101.17 (RESET)
unnamed: U101.1 (CANTX), U102.1 (TXD)
unnamed: U101.2 (CANRX), U102.4 (RXD)
SCK: U4.23 (GPIO11_(SCLK)), U101.13 (SCK)
SCL: R5.2, U1.3 (Scl), U2.3 (scl), U3.16 (SCL), U4.5 (GPIO3_(SCL))
SDA: R2.2, U1.4 (Sda), U2.4 (sda), U3.15 (SDA), U4.3 (GPIO2_SDA)

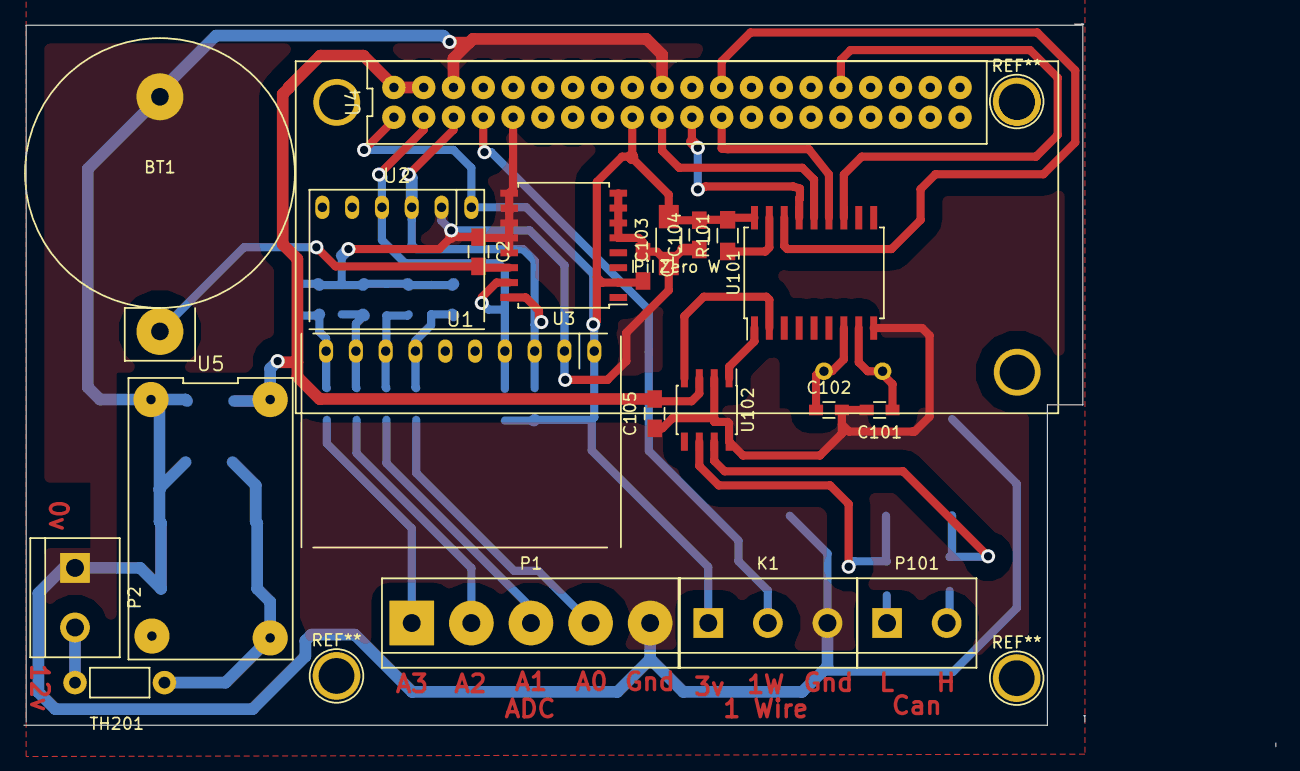
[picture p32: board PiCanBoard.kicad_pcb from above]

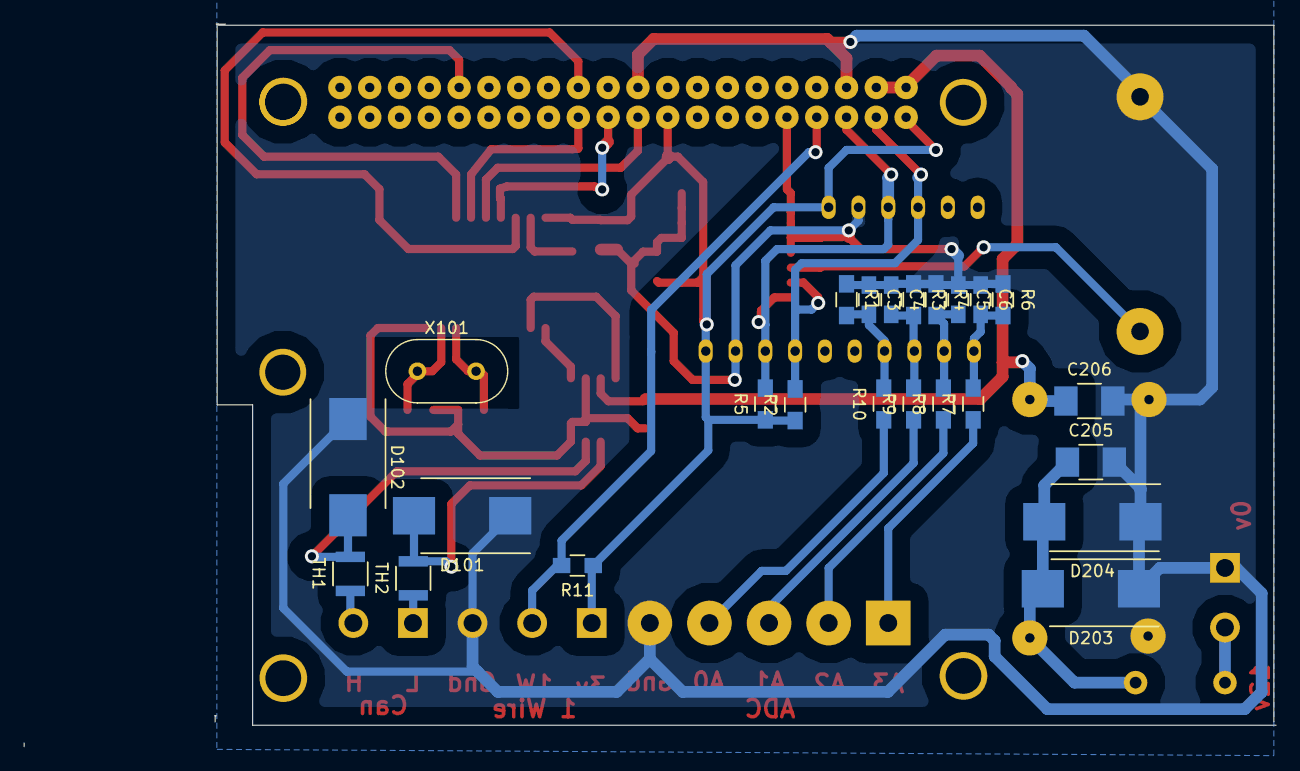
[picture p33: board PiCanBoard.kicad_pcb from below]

Board: 2 copper layers, 106.7 x 61.6 mm, 45 parts (24 on the bottom side), 31 nets.

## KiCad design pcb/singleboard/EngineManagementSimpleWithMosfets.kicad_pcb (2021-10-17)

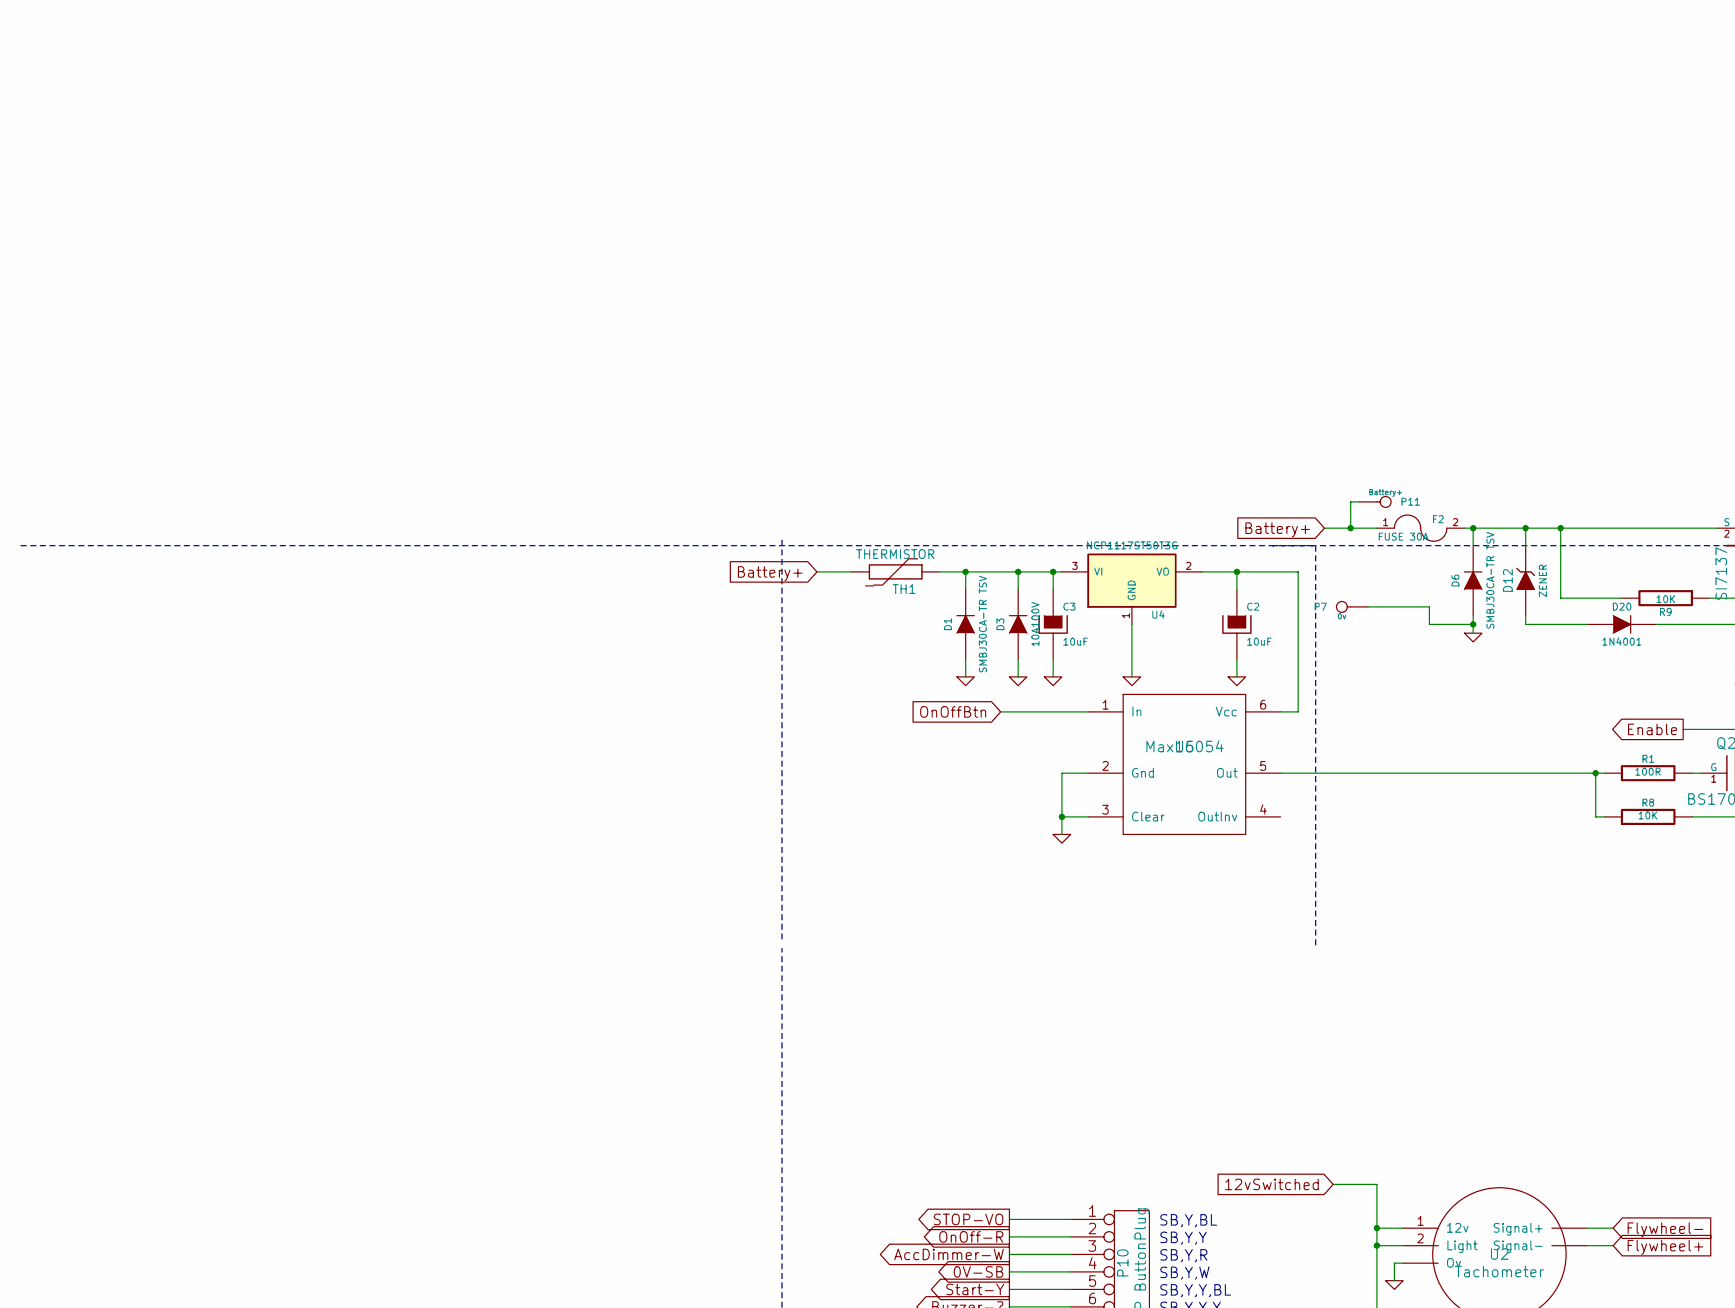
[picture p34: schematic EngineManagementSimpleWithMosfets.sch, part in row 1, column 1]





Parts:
C1: 10nF; C_0805_HandSoldering
C2, C3: 10uF; C_Radial_D8_L11.5_P3.5
D1, D6, D11, D13, D19: SMBJ30CA-TR TSV; DO-214AB_Handsoldering
D2: ChargeWarn; R_0805_HandSoldering
D3: 10A100V; Resistor_Horizontal_RM7mm
D4: TempWarn; R_0805_HandSoldering
D5: OilWarn; R_0805_HandSoldering
D7, D18: 5A 600V; Diode_P600_Vertical_AnodeUp
D8: 10A 600V; Diode_P600_Vertical_KathodeUp
D9: 1A 40V; DO-214AB
D10: 10A 600V; Diode_P600_Vertical_AnodeUp
D12, D15, D16: ZENER; D_SOD-123
D14: PowerOn; R_0805_HandSoldering
D17: 10V Zeener; D_SOD-123
D20, D21, D22, D23: 1N4001; D_SOD-123
F1: FUSE 5A; BladeFuse-CarType
F2: FUSE 30A; BladeFuse-CarType
F3: 6A Breaker
F4, F5: 6A breaker
F6, F8: FUSE 40A; BladeFuse-CarType
F7: FUSE 15A; BladeFuse-CarType
P1: VPButtons; bornier5
P2: ToEngine; bornier6
P3: StarterSolenoidT30; CrimpBlade
P4: StopSolenoid; CrimpBlade
P5: 12VSwitchedPower; CrimpBlade
P6: GlowPlugs; CrimpBlade
P7: 0v; CrimpBlade
P8: VP EnginePlug
P9: VP MultiLinkPlug
P10: VP ButtonPlug
P11: Battery+; CrimpBlade
Q1, Q5, Q6: BC807; SOT-23_Handsoldering
Q2: BS170; SOT-23_Handsoldering
Q3, Q4, Q7, Q8, Q9: SI7137; Si7137PowerPak
Q11, Q13, Q15: BS250P; SOT-23_Handsoldering
R1, R15, R24, R31: 100R; R_0805_HandSoldering
R2: 330R; R_0805_HandSoldering
R3, R18, R20, R27, R28: 2.2K; R_0805_HandSoldering
R4, R5, R6, R8, R9, R17, R21, R25: 10K; R_0805_HandSoldering
R7: 10R; Resistor_Horizontal_RM20mm
R10, R33, R34, R35: 220R; R_0805_HandSoldering
R11, R13, R14, R16, R19, R22, R23, R26: 1K; R_0805_HandSoldering
R12: 10M; R_0805_HandSoldering
RV1: 20K; Potentiometer_Bourns_3296W_3-8Zoll_Inline_ScrewUp
SP1: Buzzer
SW1: ON/OFF
SW2: Start
SW3: Stop
SW4: Glow
SW5: Neutral
TH1: THERMISTOR; Resistor_Horizontal_RM7mm
U1: LM358; DIP-8_W7.62mm_LongPads
U2: Tachometer
U3: WaterTemp
U4: NCP1117ST50T3G; SOT-223-3Lead_TabPin2
U5: Max16054; SOT-23-6_Handsoldering

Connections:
12vSwitched: D2.1 (A), D4.1 (A), D5.1 (A), F1.2, P2.5, Q1.2 (E), Q5.2 (E), Q6.2 (E), R3.1, R7.2, R18.2, R21.2, R22.1, RV1.1, U1.8 (V+), U2.1 (12v), U2.2 (Light), U3.1 (12v), U3.2 (Light); also elsewhere on the board
AlternatorExcitation: D9.2 (K), P2.1
Battery+: F2.1, F6.1, F7.1, F8.1, P11.1, TH1.2
Buzzer: P2.3, Q1.3 (C), Q5.3 (C), Q6.3 (C)
CoolantTemp: C1.2, P2.4, R4.2, R22.2, U3.~ (Ov); also elsewhere on the board
Enable: Q2.3 (D), R10.1, R33.1, R34.1, R35.1
GND: C1.1, C2.2, C3.2, D1.1 (A), D3.1 (A), D6.1 (A), D7.1 (A), D10.1 (A), D11.1 (A), D13.1 (A), D18.1 (A), D19.1 (A), P1.5, P2.6, P7.1, Q2.2 (S), R2.2, R8.2, R23.2, SP1.2, SW1.1, SW2.1, SW3.1, SW4.1, U1.4 (V-), U2.~ (Ov), U3.~ (Ov), U4.1 (GND), U5.2 (Gnd), U5.3 (Clear); also elsewhere on the board
GlowBtn: P1.2, R24.2, R27.1
GlowPlugs: P6.1, Q7.3 (D), Q8.3 (D)
unnamed: C2.1, U4.2 (VO), U5.6 (Vcc)
unnamed: C3.1, D1.2 (K), D3.2 (K), TH1.1, U4.3 (VI)
unnamed: D2.2 (K), R11.1
unnamed: D4.2 (K), R16.2
unnamed: D5.2 (K), R19.1
unnamed: D8.1 (A), Q4.3 (D)
unnamed: D9.1 (A), R6.2, R7.1, R11.2
unnamed: D11.2 (K), D16.2 (K), F6.2, Q7.2 (S), Q8.2 (S), R14.2, R27.2
unnamed: D12.1 (A), D20.1 (A)
unnamed: D6.2 (K), D12.2 (K), F2.2, Q3.2 (S), R9.2
unnamed: D13.2 (K), D15.2 (K), F7.2, Q4.2 (S), R13.1, R25.2
unnamed: D14.1 (A), D18.2 (K), F1.1, F3.1, F4.1, F5.1, P5.1, Q3.3 (D)
unnamed: D14.2 (K), R23.1
unnamed: D15.1 (A), D21.1 (A)
unnamed: D16.1 (A), D23.1 (A)
unnamed: D17.1 (A), D22.1 (A)
unnamed: D17.2 (K), D19.2 (K), F8.2, Q9.2 (S), R26.2, R28.2
unnamed: D20.2 (K), Q3.1 (G), R9.1, R10.2
unnamed: D21.2 (K), Q4.1 (G), Q11.2 (S), R13.2
unnamed: D22.2 (K), Q9.1 (G), Q13.2 (S), R26.1
unnamed: D23.2 (K), Q7.1 (G), Q8.1 (G), Q15.2 (S), R14.1
unnamed: P9.1, P9.2
unnamed: P9.3, P9.5
unnamed: P10.1, SW3.2
unnamed: P10.2, SW1.2
unnamed: P10.3, SW4.2
unnamed: P10.5, SW5.2
unnamed: P10.6, SP1.1
unnamed: Q1.1 (B), R3.2, R6.1
unnamed: Q2.1 (G), R1.2
unnamed: Q5.1 (B), R17.2, R18.1
unnamed: Q6.1 (B), R20.1, R21.1
unnamed: Q11.1 (G), R15.1
unnamed: Q11.3 (D), R33.2
unnamed: Q13.1 (G), R31.1
unnamed: Q13.3 (D), R34.2
unnamed: Q15.1 (G), R24.1
unnamed: Q15.3 (D), R35.2
unnamed: R1.1, R8.1, U5.5 (Out)
unnamed: R2.1, R5.2, RV1.2
unnamed: R4.1, U1.3 (+)
unnamed: R12.1, R16.1, R17.1, U1.1
unnamed: R5.1, R12.2, U1.2 (-)
unnamed: SW2.2, SW5.1
OilSwitch: P2.2, R19.2, R20.2
OnOffBtn: P1.4, U5.1 (In)
StartBtn: P1.3, R28.1, R31.2
StarterSolenoidT30: D7.2 (K), P3.1, Q9.3 (D)
StopBtn: P1.1, R15.2, R25.1
StopSolenoid: D8.2 (K), D10.2 (K), P4.1

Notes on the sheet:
40A
10A
Standard Volvo Penta Plugs SB= Black, GR= Grey, W= White R= Red, BN= Brown, Y= Yellow P= Pink, BL= Blue, GN= Green OR= Orange, VO= Violet
Wire codes. SB,BL,Y,R,W Code always starts with SB. Second code marks the connector, 3rd and 4th code marks the wire. All these wires will probably be in a single conduit.
SB,Y,Y,Y
SB,Y,Y,BL
SB,BL,BL,Y
SB,BL,BL,BL
SB,SB,SB,W
SB,SB,SB,R
SB,SB,SB,Y
SB,SB,SB,BL
SB,Y,W
SB,Y,R
SB,Y,Y
SB,Y,BL
SB,BL,W
SB,BL,R
SB,BL,Y
SB,BL,BL
SB,SB,W
SB,SB,R
SB,SB,Y
SB,SB,BL
Cockpit
ControlBoard
WiringWithControlBoard

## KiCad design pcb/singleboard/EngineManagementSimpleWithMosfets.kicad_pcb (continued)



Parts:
C101, C102: 22pF; R_0603_HandSoldering
C103: 10uF; R_1206_HandSoldering
C104, C105: 100nF; C_0805_HandSoldering
C201, C202: 1uF; C_1210
C203, C204, C212: 1nF; C_0805_HandSoldering
C205: 100uF; C_Radial_D8_L11.5_P3.5
C206, C207, C208, C209, C210, C211: 10nF; C_0805_HandSoldering
D101, D102, D203: SMBJ30CA-TR TSV; DO-214AB_Handsoldering
D201, D202: 1N5819; D_SOD-123
D204: 1N5819; Resistor_Horizontal_RM7mm
K201: Temps; bornier3
K202: FuelCool; bornier3
K203: FuelCoolAlt; bornier3
K204: Supply; bornier3
P101: CanBus; bornier2
R101: 10K; R_0805_HandSoldering
R201, R202, R220: 22K; R_0805_HandSoldering
R203, R204, R219: 1M; R_0805_HandSoldering
R205, R207, R218: 470K; R_0805_HandSoldering
R206, R213, R214: 1K; R_0805_HandSoldering
R208, R209, R210, R211, R212, R221, R222: 100K; R_0805_HandSoldering
R215, R216, R217: 4.7K; R_0805_HandSoldering
TH201: 500mA Thermistor; Resistor_Horizontal_RM7mm
U101: MCP2515; SOIC-18W_7.5x11.6mm_Pitch1.27mm
U102: TJA1050; SOIC-8_3.9x4.9mm_Pitch1.27mm
U201: MCP2515Shield; MCP2515Board
U202: LM7808CT; TO-263-3Lead
U203: ArdinoMinPro; ArduinoProMini
U204: LM358; DIP-8_W7.62mm_LongPads
X101: 8MHz; Resonator-2pin_w10.0mm_h5.0mm

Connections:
5V150mA: C103.2, C104.2, C105.2, R101.2, R215.1, R216.1, R217.1, U101.18 (Vdd), U102.3 (Vcc), U201.7 (Vcc), U203.21 (VCC), U204.8 (V+)
8V: C206.1, R213.1, R214.1, U202.3 (OUT), U203.24 (RAW)
12vSwitched: K204.2 (PM), R204.2, TH201.2; also elsewhere on the board
AlternatorB+: K202.1, R219.1
CANCS: U101.16 (CS), U201.5 (CS), U203.13 (D10)
CoolantTemp: C207.1, K203.1, R212.2, R213.2; also elsewhere on the board
Flywheel+: K202.2 (PM), R201.1
Flywheel-: K202.3, R202.1
FuelLevel+: C208.1, K203.2 (PM), R211.2, R214.2
GND: C101.2, C102.2, C103.1, C104.1, C105.1, C201.2, C202.2, C203.2, C204.2, C205.2, C206.2, C207.2, C208.2, C209.2, C210.2, C211.2, C212.2, D101.1 (A), D102.1 (A), D201.2 (K), D202.1 (A), D203.1 (A), D204.1 (A), K203.3, K204.1, R202.2, R205.1, R206.2, R207.1, R218.1, R221.1, U101.9 (GND), U102.2 (GND), U102.8 (S), U201.6 (GND), U202.2 (GND), U203.4 (GND), U203.23 (GND), U203.31 (GND), U204.4 (V-); also elsewhere on the board
MISO: U101.15 (SO), U201.4 (SO), U203.15 (MISO)
MOSI: U101.14 (SI), U201.3 (SI), U203.14 (MOSI)
NTC1: C209.1, K201.3, R210.2, R215.2
NTC2: C210.1, K201.2 (PM), R209.2, R216.2
NTC3: C211.1, K201.1, R208.2, R217.2
unnamed: C101.1, U101.8 (OSC1), X101.1
unnamed: C102.1, U101.7 (OSC2), X101.2
unnamed: C201.1, D201.1 (A), D202.2 (K), R201.2, R206.1, R220.2, R222.2, U204.3 (+)
unnamed: C202.1, R222.1, U204.2 (-)
unnamed: C203.1, R204.1, R205.2, U203.A7
unnamed: C204.1, R203.1, R207.2, U203.A6
unnamed: C205.1, D203.2 (K), D204.2 (K), TH201.1, U202.1 (IN)
unnamed: C212.1, R218.2, R219.2, U203.A5 (SCL/A5)
unnamed: D101.2 (K), P101.2 (PM), U102.6 (CanH)
unnamed: D102.2 (K), P101.1, U102.7 (CanL)
unnamed: R101.1, U101.17 (RESET)
unnamed: R208.1, U203.A4 (SDA/A4)
unnamed: R209.1, U203.20 (A3)
unnamed: R210.1, U203.19 (A2)
unnamed: R211.1, U203.18 (A1)
unnamed: R212.1, U203.17 (A0)
unnamed: U101.1 (CANTX), U102.1 (TXD)
unnamed: U101.2 (CANRX), U102.4 (RXD)
RPMPulse: R220.1, R221.2, U203.5 (D2), U204.1
SCK: U101.13 (SCK), U201.2 (Sck), U203.16 (SCK)
ServiceBattery+: K204.3, R203.2

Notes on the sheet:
Monitoring
Fuel Sensor 0R == Empty 190R == Full Supply 8V Use 1K, Full 1.2V empty 0v Current max 8mA, 64mW
Coolant Sensor With 8V supply R23 at 1K 120C == 22R 0C = 1743R 120C == 8*22/(1000+22)=0.17V 80C = 8*70/1000+70)=0.52V 50C = 8*197/1000+ 197)=1.3V 8mA
Can board with trancever built in. Using Onboard connector
ProMini only has interrupts on pins 2 and 3 There is a 10K pullup on the reset on board.
Signal at idle is 32v pkp, 415Hz, and rises from there as the engine speed picks up. At idle the power disipated in the diodes is uW. At 3KHz, 150V pkp currents in diodes a 1mA or less At 415Hz 32v voltage across caps is < 20v
NTC MF52-10K 100K at 0C 5*100/(100+10)=4.5v 25K at 5C 5*25/(25+10)=3.5v 10K at 20C 5*10/(10+10)=2.5v 506R at 110C 5*0.506/(0.506+10)=0.179v x =22K
Coolant Sensor With 12V supply R23 fitted externally. 120C == 22R 0C = 1743R 120C == 12*22/(1000+22)=0.25V 80C = 12*70/1000+70)=0.78V 50C = 12*197/(1000+197)=1.97 20C = 12*677/(1000+677)=4.8 11mA
Flywheel or Alternator W+ Input
Op Amp configured as Schmitt Trigger with control over hysterisis. The RC on the -Vin on the op amp automatically adjusts bias of the input signal to ensure switching always occurs at the mean voltage of the input signal. RC is set so it take a few cycles at low frequency and perhaps 100 at KHz
Threshold Peak to Peak voltages to trigger square wave out. 4KHz >= 80V 3KHz >= 60V 2KHz >= 40V 1KHz >= 20V 500Hz >= 13V 400Hz >= 12V 200Hz >= 10V
Do not add R213 if 1K is on relay board



Board: 2 copper layers, 150.0 x 100.0 mm, 147 parts (3 on the bottom side), 84 nets.

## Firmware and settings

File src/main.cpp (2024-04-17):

#include <Arduino.h>
#include "enginesensors.h"
#include "SmallNMEA2000.h"


#define RAPID_ENGINE_UPDATE_PERIOD 500
#define ENGINE_UPDATE_PERIOD 1000
#define VOLTAGE_UPDATE_PERIOD 999
#define FUEL_UPDATE_PERIOD 4900
#define TEMPERATURE_UPDATE_PERIOD 4850

#define ENGINE_INSTANCE 0
#define ENGINE_BATTERY_INSTANCE 0
// treating the alternator as a battery its possible to monitor temperature.
#define ALTERNATOR_BATTERY_INSTANCE 2
// Now using a dedicated shunt for service battery #define SERVICE_BATTERY_INSTANCE 2
#define FUEL_LEVEL_INSTANCE 0
#define FUEL_TYPE 0   // diesel

const SNMEA2000ProductInfo productInfomation PROGMEM={
                                       1300,                        // N2kVersion
                                       44,                         // Manufacturer's product code
                                       "EMS",    // Manufacturer's Model ID
                                       "1.2.3.4 (2023-05-16)",     // Manufacturer's Software version code
                                       "5.6.7.8 (2017-06-11)",      // Manufacturer's Model version
                                       "0000001",                  // Manufacturer's Model serial code
                                       0,                           // SertificationLevel
                                       1                            // LoadEquivalency
};
const SNMEA2000ConfigInfo configInfo PROGMEM={
      "Engine Monitor",
      "Luna Technical Area",
      "https://github.com/ieb/EngineManagement"
};


const unsigned long txPGN[] PROGMEM = { 
    127488L, // Rapid engine ideally 0.1s
    127489L, // Dynamic engine 0.5s
    127505L, // Tank Level 2.5s
    130316L, // Extended Temperature 2.5s
    127508L,
  SNMEA200_DEFAULT_TX_PGN
};
const unsigned long rxPGN[] PROGMEM = { 
  SNMEA200_DEFAULT_RX_PGN
};

SNMEA2000DeviceInfo devInfo = SNMEA2000DeviceInfo(
  222,   // device serial number
  140,  // Engine
  50 // Propulsion
);


#define DEVICE_ADDRESS 24
#define SNMEA_SPI_CS_PIN 10

EngineMonitor engineMonitor = EngineMonitor(DEVICE_ADDRESS,
  &devInfo,
  &productInfomation, 
  &configInfo, 
  &txPGN[0], 
  &rxPGN[0],
  SNMEA_SPI_CS_PIN);

EngineSensors sensors(DEFAULT_FLYWHEEL_READ_PERIOD,
  DEFAULT_FUEL_READ_PERIOD,
  DEFAULT_COOLANT_READ_PERIOD,
  DEFAULT_VOLTAGE_READ_PERIOD,
  DEFAULT_NTC_READ_PERIOD);

void sendRapidEngineData() {
  static unsigned long lastRapidEngineUpdate=0;
  unsigned long now = millis();
  if ( now-lastRapidEngineUpdate > RAPID_ENGINE_UPDATE_PERIOD ) {
    lastRapidEngineUpdate = now;
    engineMonitor.sendRapidEngineDataMessage(ENGINE_INSTANCE, sensors.getEngineRPM());
  }
}


void sendEngineData() {
  static unsigned long lastEngineUpdate=0;
  unsigned long now = millis();
  if ( now-lastEngineUpdate > ENGINE_UPDATE_PERIOD ) {
    lastEngineUpdate = now;
    engineMonitor.sendEngineDynamicParamMessage(ENGINE_INSTANCE,
        sensors.getEngineSeconds(),
        sensors.getCoolantTemperatureK(),
        sensors.getAlternatorVoltage(),
        0, // status1
        0, // status2
        SNMEA2000::n2kDoubleNA, // engineOilPressure
        sensors.getAlternatorTemperatureK() // alterator temperature as nengineOil temperature
        );
  }
}


void sendVoltages() {
  static unsigned long lastVoltageUpdate=0;
  static byte sid = 0;
  unsigned long now = millis();
  if ( now-lastVoltageUpdate > VOLTAGE_UPDATE_PERIOD ) {
    lastVoltageUpdate = now;
    // because the engine monitor is not on all the time, the sid and instance ids of these messages has been shifted
    // to make space for sensors that are on all the time, and would be used by default
    // engineMonitor.sendDCBatterStatusMessage(SERVICE_BATTERY_INSTANCE, sid, sensors.getServiceBatteryVoltage());
    engineMonitor.sendDCBatterStatusMessage(ENGINE_BATTERY_INSTANCE, sid, sensors.getEngineBatteryVoltage());
    engineMonitor.sendDCBatterStatusMessage(ALTERNATOR_BATTERY_INSTANCE, sid, 
        sensors.getAlternatorVoltage(),
        sensors.getAlternatorTemperatureK()
        );
    sid++;
  }
}

void sendFuel() {
  static unsigned long lastFuelUpdate=0;
  unsigned long now = millis();
  if ( now-lastFuelUpdate > FUEL_UPDATE_PERIOD ) {
    lastFuelUpdate = now;
    engineMonitor.sendFluidLevelMessage(FUEL_TYPE, FUEL_LEVEL_INSTANCE, sensors.getFuelLevel(), sensors.getFuelCapacity());

  }
}

void sendTemperatures() {
  static unsigned long lastTempUpdate=0;
  static byte sid = 0;
  unsigned long now = millis();
  if ( now-lastTempUpdate > TEMPERATURE_UPDATE_PERIOD ) {
    lastTempUpdate = now;
    engineMonitor.sendTemperatureMessage(sid, 0, 14, sensors.getExhaustTemperatureK());
    engineMonitor.sendTemperatureMessage(sid, 1, 3, sensors.getEngineRoomTemperatureK());
    engineMonitor.sendTemperatureMessage(sid, 2, 15, sensors.getAlternatorTemperatureK());
    sid++;
  }
}

void setup() {
  Serial.begin(115200);
  Serial.println(F("Luna engine monitor start"));
  while(!sensors.begin() ) {
    Serial.println(F("Failed to start Engine Sensors, retry in 5s"));
    delay(5000);
  }
  Serial.println(F("Opening CAN"));
  while (!engineMonitor.open() ) {
     Serial.println(F("Failed to start NMEA2000, retry in 5s"));
    delay(5000);
  }
  Serial.println(F("Opened, MCP2515 Operational"));
  Serial.println(F("Running..."));;
}

void loop() {
  sensors.read();
  sendRapidEngineData();
  sendEngineData();
  sendVoltages();
  sendTemperatures();
  sendFuel();
  engineMonitor.processMessages();
}

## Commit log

2021-08-16 Initial commit, v1 board running, testing
    [EngineManagement.kicad_pcb, EngineManagement.sch, EngineManagement_bom.csv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]
2021-08-20 Before using edge triggers for onoff
    [EngineManagement.sch]
2021-08-22 VP Tacho has blown Can drivers on custom ASIC, plan aborted
    [EngineManagement.sch, EngineManagementSimple.sch]
2021-09-07 Redesigned to not use VP J1939 instruments
    [EngineManagement.sch, EngineManagementSimple copy 2.sch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]
2021-09-09 NTC sensors working correctly
    [EngineManagement.sch, _saved_EngineManagement.sch]
2021-09-12 Added pdfs for reference
    [EngineManagement.kicad_pcb, EngineManagement.sch, EngineManagementSimpleWithRelays.kicad_pcb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]
2021-10-01 Added mosfet based board
    [EngineManagement.sch, EngineManagementSimpleWithMosfets.csv, EngineManagementSimpleWithMosfets.kicad_pcb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]
2021-10-17 After testing, fixed a number of things
    [EngineManagement.kicad_pcb, EngineManagement.sch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]
2021-10-25 Fixed sending product info and byte orders
    [main.cpp]
2021-10-26 Fixed masks and filters
2021-10-27 Fixed some output encoding errors
    [main.cpp]
2021-10-28 Extracted sensors into a class
2021-11-28 Istalled working version, all working, may need some adjustment on messages
    [EngineManagement.kicad_pcb, MosfetSwitch.kicad_pcb, MosfetSwitch.sch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]
2021-12-29 Dixed sequence ID errors, added dsign for PiCan board
    [PiCanBoard.kicad_pcb, PiCanBoard.sch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]
2021-12-29 Mistook instance for sid, fixed
    [main.cpp]
2022-07-15 Reorged pcbs and brought NMEA2000 improvements in from CanPressure via lib
    [EngineManagement.kicad_pcb, EngineManagement.sch, EngineManagementSimple copy 2.sch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]
2024-04-17 Fixes to output messages, and spell check
    [main.cpp]
